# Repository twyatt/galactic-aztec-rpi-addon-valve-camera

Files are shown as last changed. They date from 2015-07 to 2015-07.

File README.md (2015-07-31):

# About

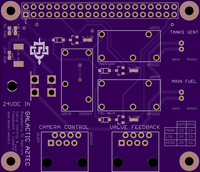
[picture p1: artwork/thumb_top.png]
OSHPark PCB Top Thumbnail

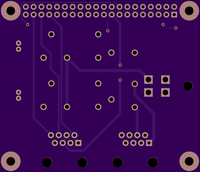
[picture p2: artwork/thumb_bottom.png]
OSHPark PCB Bottom Thumbnail


Custom Raspberry Pi Add-on board used for launching the [Galactic Aztec] rocket. The board was designed to be stackable with other add-on boards via the designated [pin configuration].

The Camera Control ethernet port was designed to activate [HackHD] cameras via the [Galactic Aztec Camera Control] \(rev2 or newer) board and can be configured to activate multiple [HackHD]s using the [Galactic Aztec Camera Control Splitter] board.

The Valve Feedback ethernet port was designed to read valve actuation status (open or close) by means of reading Reed switches (for the Main, LOX and Kerosene valves) via the [Galactic Aztec Reed Switch Interface] and [Galactic Aztec Reed Switch Splitter] boards.

Custom EagleCAD parts on this board can be found in the [SDSU Rocket Eagle Libraries].

## Wiring
The Camera Control and Valve Feedback ethernet ports adhered to the following [T-568B] wiring configurations:

### Camera Control
| Pin | Color | Function |
|:---:|:---:|:---:|
| 1 | Orange/White | In |
| 2 | Orange | Out |
| 3 | Green/White  | In |
| 4 | Blue | Out |
| 5 | Blue/White | In |
| 6 | Green | Out |
| 7 | Brown/White  | In |
| 8 | Brown | Out |

*In and Out do not have a polarity but rather are labeled to distinguish the two sides of the camera connection (used to [control the HackHD] by means of connecting `Button Input` to `Ground`).*

### Valve Feedback
| Pin | Color | Function |
|:---:|:---:|:---:|
| 1 | Orange/White | Main |
| 2 | Orange | Main |
| 3 | Green/White  | LOX |
| 4 | Blue | 3.3V |
| 5 | Blue/White | 3.3V |
| 6 | Green | LOX |
| 7 | Brown/White  | Kerosene |
| 8 | Brown | Kerosene |

# Bill of Materials
| Qty | Description | Part Number | Vendor |
|:---:|---|---:|---|
| 1 | Header Stacking 2x20 Tall 23mm | [1979] | Adafruit |
| 2 | Jack RJ45 CAT5/CAT5e | [380-1046-ND] | DigiKey  |
| 2 | Header JST PH 2mm 2-pos Right Angle PTH | [455-1719-ND] | DigiKey  |
| 1 | LED Red Vf=1.8V If=2mA 0603 | [475-1195-2-ND] | DigiKey  |
| 1 | Molex Mini Fit Jr. 4-pos Right Angle | [WM1352-ND] | DigiKey  |
| 1 | LED Red Vf=2V If=20mA 0603 | [754-1359-1-ND] | DigiKey  |
| 3 | Transistor NPN 40V 600mA SOT-23-3 | [MMBT2222ATPMSCT-ND] | DigiKey  |
| 1 | Resistor 1.8kΩ 1/4W 1% 0603 | [P1.8KBYCT-ND] | DigiKey  |
| 1 | Resistor 1.2kΩ 2W 1% 2512 | [A116034CT-ND] | DigiKey  |
| 3 | Resistor 1kΩ 1/4W 1% 0603 | [RHM1.00KADCT-ND] | DigiKey  |
| 3 | Diode 50V 1A SOD-123 | [SM4001PL-TPMSCT-ND] | DigiKey  |
| 3 | Relay 5V 5A SPST-NO (1 Form A) | [Z945-ND] | DigiKey  |

[Galactic Aztec]: http://rocket.sdsu.edu/rockets
[pin configuration]: https://docs.google.com/spreadsheets/d/1zGslKhH-ZteeA8sbbTjQlF-Neb-wJ3quIlFH6I8Cvgs/edit?usp=sharing
[HackHD]: http://hackhd.com/
[Galactic Aztec Camera Control]: https://github.com/twyatt/galactic-aztec-camera-control
[Galactic Aztec Camera Control Splitter]: https://github.com/twyatt/galactic-aztec-camera-control-splitter
[Galactic Aztec Reed Switch Interface]: https://github.com/twyatt/galactic-aztec-reed-switch-interface
[Galactic Aztec Reed Switch Splitter]: https://github.com/twyatt/galactic-aztec-reed-switch-splitter
[SDSU Rocket Eagle Libraries]: https://github.com/twyatt/SDSURocket-Eagle-Libraries
[T-568B]: https://en.wikipedia.org/wiki/TIA/EIA-568#Wiring
[control the HackHD]: http://www.hackhd.com/hiw.php
[1979]: http://www.adafruit.com/products/1979
[380-1046-ND]: http://www.digikey.com/product-detail/en/SS-7188-NF/380-1046-ND/388308
[455-1719-ND]: http://www.digikey.com/product-detail/en/S2B-PH-K-S(LF)(SN)/455-1719-ND/926626
[475-1195-2-ND]: http://www.digikey.com/product-detail/en/LS%20L29K-H1J2-1-Z/475-1195-1-ND/810356
[WM1352-ND]: http://www.digikey.com/product-search/en?x=0&y=0&lang=en&site=us&keywords=538-39-30-1040
[754-1359-1-ND]: http://www.digikey.com/product-detail/en/APG1608SURKC%2FT/754-1359-1-ND/1919171
[MMBT2222ATPMSCT-ND]: http://www.digikey.com/product-detail/en/MMBT2222A-TP/MMBT2222ATPMSCT-ND/717394
[P1.8KBYCT-ND]: http://www.digikey.com/product-detail/en/ERJ-PA3F1801V/P1.8KBYCT-ND/5036145
[A116034CT-ND]: http://www.digikey.com/product-detail/en/5-2176070-1/A116034CT-ND/4280086
[RHM1.00KADCT-ND]: http://www.digikey.com/product-detail/en/ESR03EZPF1001/RHM1.00KADCT-ND/1983752
[SM4001PL-TPMSCT-ND]: http://www.digikey.com/product-detail/en/SM4001PL-TP/SM4001PL-TPMSCT-ND/1793403
[Z945-ND]: http://www.digikey.com/product-detail/en/G6B-1114P-US-DC5/Z945-ND/148724

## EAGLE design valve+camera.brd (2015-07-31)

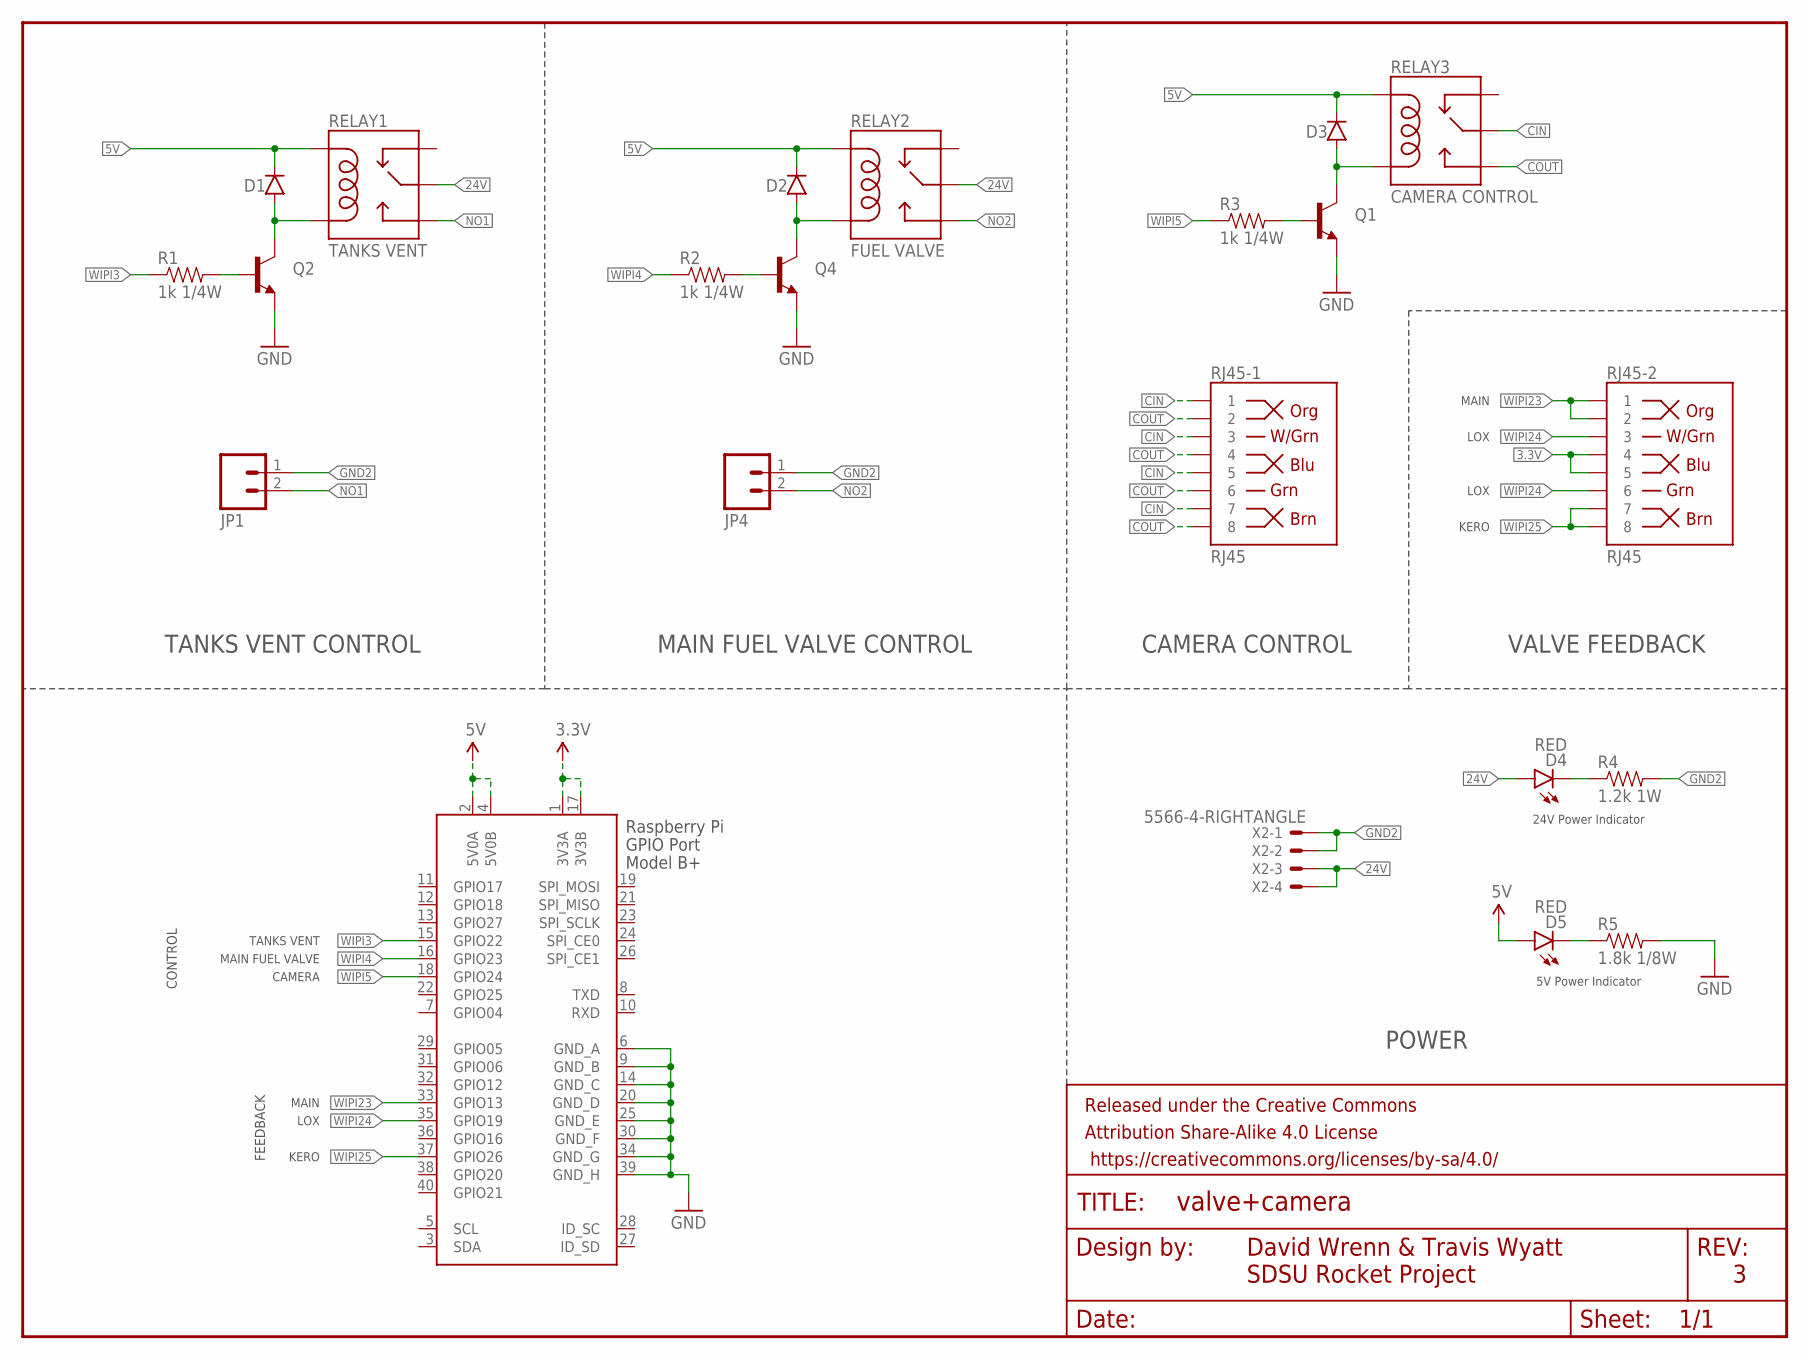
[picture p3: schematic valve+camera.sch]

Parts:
D1, D2, D3: DIODESOD123; SOD-123
D4, D5: RED; LED-0603
FRAME1: FRAME-LETTER; CREATIVE_COMMONS
JP1, JP4: M02-JST-2-PTH-NO_SILK; JST-2-PTH-NS
Q1, Q2, Q4: TRANSISTOR_NPNSOT23-3; SOT23-3
R1, R2, R3: 1k 1/4W; 0603-RES
R4: 1.2k 1W; R2512
R5: 1.8k 1/8W; 0603-RES
RELAY1: TANKS VENT; RELAY-G5Q
RELAY2: FUEL VALVE; RELAY-G5Q
RELAY3: CAMERA CONTROL; RELAY-G5Q
RJ45-1, RJ45-2: RJ45; RJ45-8
X1: RASPI_BOARD_B+#_H; RASPI_BOARD_B+HAT
X2: 5566-4-RIGHTANGLE; 5566-4

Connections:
3.3V: RJ45-2.4, RJ45-2.5, X1.1 (3V3A), X1.17 (3V3B)
5V: D1.C, D2.C, D3.C, D5.A, RELAY1.5 (COIL1), RELAY2.5 (COIL1), RELAY3.5 (COIL1), X1.2 (5V0A), X1.4 (5V0B)
24V: D4.A, RELAY1.2 (MAIN), RELAY2.2 (MAIN), X2.3, X2.4
CIN: RELAY3.2 (MAIN), RJ45-1.1, RJ45-1.3, RJ45-1.5, RJ45-1.7
COUT: RELAY3.3 (NO), RJ45-1.2, RJ45-1.4, RJ45-1.6, RJ45-1.8
GND: Q1.2 (E), Q2.2 (E), Q4.2 (E), R5.2, X1.6 (GND_A), X1.9 (GND_B), X1.14 (GND_C), X1.20 (GND_D), X1.25 (GND_E), X1.30 (GND_F), X1.34 (GND_G), X1.39 (GND_H)
GND2: JP1.1, JP4.1, R4.2, X2.1, X2.2
unnamed: D4.C, R4.1
unnamed: D5.C, R5.1
unnamed: Q2.1 (B), R1.2
unnamed: D1.A, Q2.3 (C), RELAY1.1 (COIL2)
unnamed: Q1.1 (B), R3.2
unnamed: D3.A, Q1.3 (C), RELAY3.1 (COIL2)
unnamed: Q4.1 (B), R2.2
unnamed: D2.A, Q4.3 (C), RELAY2.1 (COIL2)
NO1: JP1.2, RELAY1.3 (NO)
NO2: JP4.2, RELAY2.3 (NO)
WIPI3: R1.1, X1.15 (GPIO22)
WIPI4: R2.1, X1.16 (GPIO23)
WIPI5: R3.1, X1.18 (GPIO24)
WIPI23: RJ45-2.1, RJ45-2.2, X1.33 (GPIO13)
WIPI24: RJ45-2.3, RJ45-2.6, X1.35 (GPIO19)
WIPI25: RJ45-2.7, RJ45-2.8, X1.37 (GPIO26)

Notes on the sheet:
CAMERA CONTROL
POWER
David Wrenn & Travis Wyatt
SDSU Rocket Project
24V Power Indicator
5V Power Indicator
VALVE FEEDBACK
TANKS VENT CONTROL
MAIN FUEL VALVE CONTROL
LOX
MAIN
KERO
TANKS VENT
MAIN FUEL VALVE
CAMERA
CONTROL
FEEDBACK

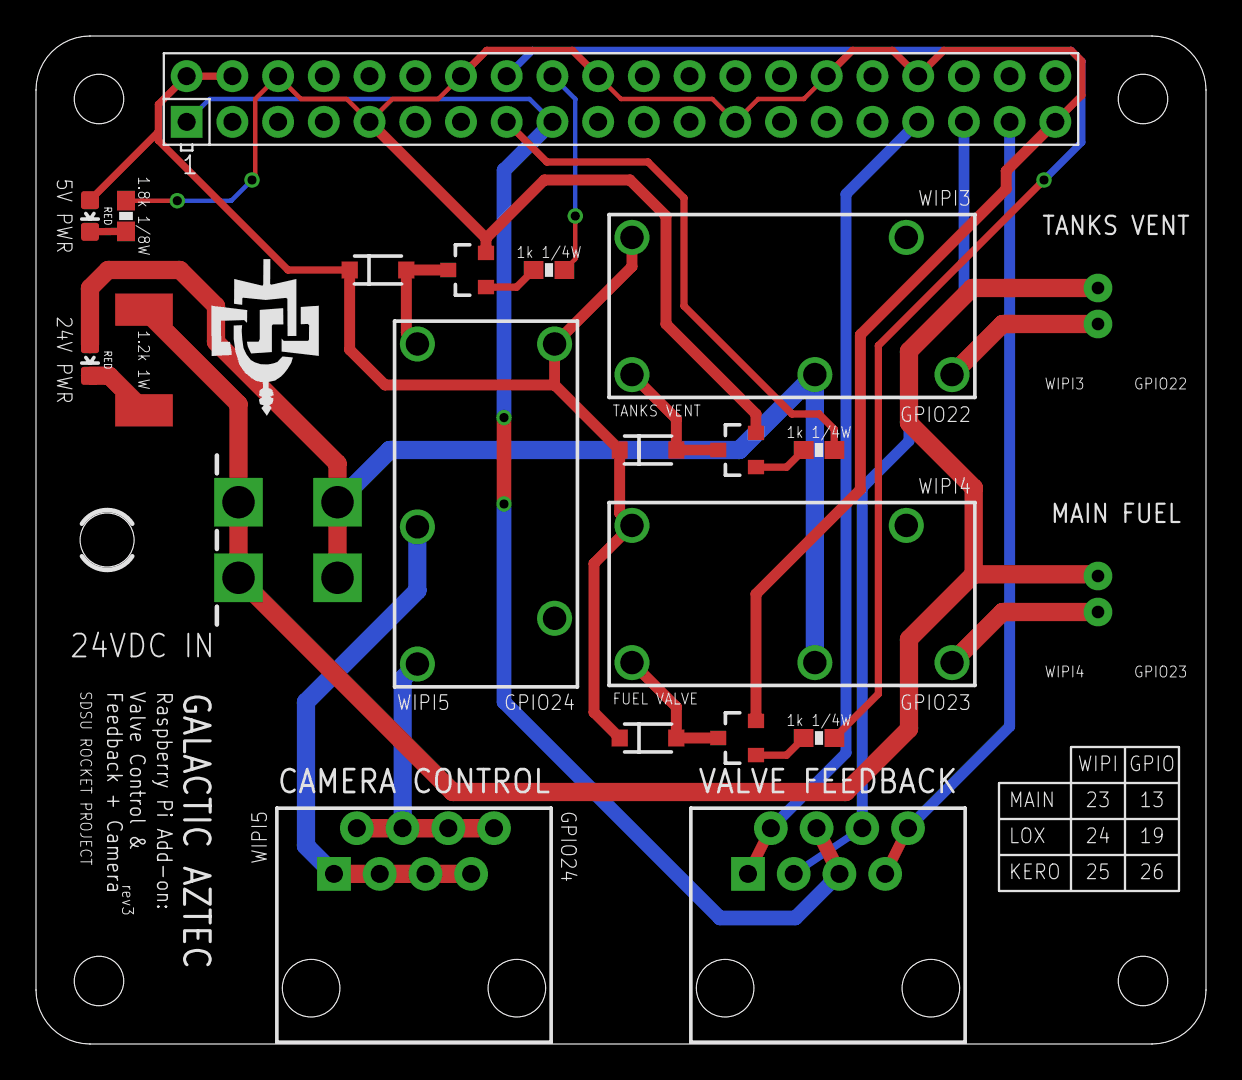
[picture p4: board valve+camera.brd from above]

Board: 2 copper layers, 65.0 x 56.0 mm, 23 parts (0 on the bottom side), 23 nets.

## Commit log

2015-07-30 Update camera control wiring and relay components
    Updated the components driving the relays to be SMD rather than PTH.
    The camera control wiring was updated to have relay activating HackHDs
    to be located on this board rather than being located on each Camera
    Control board (this means that this board is no longer compatible with
    rev1 of the Camera Control board and now requires rev2 or newer).
    [valve+camera.brd, valve+camera.sch]
2015-07-31 Fix feedback port and power thru hole size
    Feedback ethernet port was fixed by adding a missing trace.
    The 24VDC in thru hole size diameter was increased to adhere to the
    datasheet's specifications.
    The JST plugs used for valve actuation (tanks vent and main fuel) were
    change from SMD to PTH as we had problems with the SMD connectors
    breaking off when connecting or disconnecting the plugs.
    [valve+camera.brd, valve+camera.sch]

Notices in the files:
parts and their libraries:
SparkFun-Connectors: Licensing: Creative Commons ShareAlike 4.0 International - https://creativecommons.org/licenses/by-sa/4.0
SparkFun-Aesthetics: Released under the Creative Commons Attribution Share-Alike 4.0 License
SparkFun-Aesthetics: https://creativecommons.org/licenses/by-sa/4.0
